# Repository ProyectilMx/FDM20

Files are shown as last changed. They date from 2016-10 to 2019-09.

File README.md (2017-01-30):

# FDM20
-This work is licensed under the Creative Commons Attribution-NonCommercial-NoDerivatives 4.0 International License.

-Esta obra está sujeta a la licencia Reconocimiento-NoComercial 4.0 Internacional de Creative Commons. Para ver una copia de esta licencia, visite https://creativecommons.org/licenses/by-nc-sa/4.0/

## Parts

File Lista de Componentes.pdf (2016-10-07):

Qty. | Nombre | Descripción | Categoría | Qty. | Nombre | Categoría
1 | Arduino Mega | Circuito de Control | Electrónica | 2 | PortaBaleroY | Impresión 3D
1 | RAMPS | Shield para Arduino | Electrónica | 4 | SoporteGuíaY | Impresión 3D
4 | A4988 | Drivers para Motor a Pasos | Electrónica | 1 | PortaMotorX | Impresión 3D
1 | SmartController | Pantalla LCD con perilla y lector de SD | Electrónica | 1 | ContraEjeX | Impresión 3D
3 | Endstop | Sensor de Final de Carrera | Electrónica | 2 | GuíasEjeZ | Impresión 3D
1 | Cama Caliente | Cama Caliente | Electrónica | 4 | PortaBaleroZ | Impresión 3D
1 | Fuente de Alimentación | Fuente de 12V a 30A 360W | Electrónica | 1 | CarroExtrusor | Impresión 3D
1 | Extensión USB | Extensión USB B de .5 m | Electrónica | 1 | PivotePortaTornillos | Impresión 3D
1 | Termistor | Termistor de 100KOhms | Electrónica | 1 | TapaTobera | Impresión 3D
2 | Cable Termistor | Cable Morado AWG22 | Electrónica | 1 | ContraPivote | Impresión 3D
1 | Switch Encendido | Switch LED 12V de 127V | Electrónica | 1 | Brazo | Impresión 3D
1 | Conector Interlock | Conector Alimentación | Electrónica | 1 | SmartController | Impresión 3D
3 | Zapatas Conector Interlock | Zapatas cable AWG20 para Conector Interloc | Electrónica | 1 | PortaSpool | Impresión 3D
3 | Zapatas Switch Encendido | Zapatas cable AWG20 para Switch Encendid | Electrónica | 2 | Separador Endstops | Impresión 3D
13 | Zapatas Fuente | Zapatas para Fuente de Alimentación,RAMP | Electrónica | 4 | SeguroGuiaZ | CorteLaser MDF
1 | Cable Tierra Conector-Fuente | Cable Negro AWG20 de 8 cm | Electrónica | 2 | MarcoSoporteLaterialInferior | CorteLaser MDF
1 | Cable Neutro Conector-Fuent | Cable Negro AWG20 de 9 cm | Electrónica | 2 | MarcoSoporteLaterialSuperio | CorteLaser MDF
1 | Cable Línea Conector-Switch | Cable Rojo AWG20 de 23 cm | Electrónica | 1 | BasePrincipal | CorteLaser MDF
1 | Cable Línea Switch-Fuente | Cable Rojo AWG20 de 24 cm | Electrónica | 1 | PanelFrontal | CorteLaser MDF
1 | Cable Neutro Switch-Fuente | Cable Negro AWG20 de 23 cm | Electrónica | 1 | PanelTrasero | CorteLaser MDF
2 | Cable Bicolor Fuente-RAMPS | Cable Bicolor AWG20 de 25 cm | Electrónica | 1 | PanelIzquierdo | CorteLaser MDF
1 | Household Dupont Doble | Household doble dupont AWG22 | Electrónica | 1 | PanelDerecho | CorteLaser MDF
2 | Dupont | Dupont AWG22 | Electrónica | 1 | MarcoSoporteFrontal | CorteLaser MDF
3 | Cables Endstops | Cable para Endstop | Electrónica | 1 | MarcoSoporteSensor | CorteLaser MDF
3 | Cable NEMA17 | Cable para NEMA17 corto | Electrónica | 1 | BasePrincipal Superior | CorteLaser MDF
1 | Cable NEMA17 | Cable para NEMA17 mediano | Electrónica | 1 | Base Madera Cama | CorteLaser MDF
1 | Cable NEMA17 | Cable para NEMA17 largo | Electrónica | 1 | PortaMotorY | CorteLaser MDF
1 | Cable Bicolor CamaCaliente | Cable Bicolor AWG20 | Electrónica | 1 | PortaMotorY Refuerzo | CorteLaser MDF
1 | Ventilador | Ventilador de 12V d 40mmx40mm | Electromecánica | 1 | PortaMotorY Lateral1 | CorteLaser MDF
5 | NEMA17 | Motor a Pasos NEMA 17 | Electromecánica | 1 | PortaMotorY Lateral2 | CorteLaser MDF
1 | Morral | Morral de Entrega para Kits | Kit | 4 | SeguroBanda | CorteLaser MDF
1 | HotEnd | HotEnd para extrusor | Electromecánica
12 | Rodamientos Lineales | Rodamiento Lineal LM8UU | Mecánica
3 | Balero 623 | Balero 623 | Mecánica | Qty. | Tornillería
1 | Balero 624 | Balero 624 | Mecánica | 9 | M3x30
2 | Polea Dentada | Polea Dentada T2 16 dientes 5 mm | Mecánica | 110 | Tuerca M3
1 | Banda X | Banda T2 corta | Mecánica | 10 | Tuerca M3 Seguridad
1 | Banda Y | Banda T2 larga | Mecánica | 81 | M3x16
2 | Guías Y | Guía de Acero Inoxidable de 8 mm 272 mm | Mecánica | 138 | Rondana M3
2 | Guías X | Guía de Acero Inoxidable de 8 mm 384 mm | Mecánica | 3 | M3x12
2 | Guías Z | Guía de Acero Inoxidable de 8 mm 412 mm | Mecánica | 16 | M3x10
2 | Cople Flexible Z | Cople Flexible de 5 - 8 mm | Mecánica | 8 | M3x40
4 | Resortes #26 | Resortes #26 para cama caliente | Mecánica | 6 | Rondana M3 Grande
1 | Vidrio | Vidrio de 3mm de 21.5 x 20 cm | Mecánica | 7 | M3x20
2 | Esparrágo Acero Inoxidable | Esparrago de Acero Inoxidable de 385 mm | Mecánica | 14 | M3x25
1 | Engrane Estriado | Engrane Estriado para el Extrusor | Mecánica | 1 | Tuerca M4
2 | Resortes #131 | Resortes #131 para Extrusor | Mecánica | 1 | M4x16
1 | Manguera Teflon | Manguera de Teflon de 3mm | Mecánica | 2 | M3x6
3 | Grapas Manguera | Grapas para manguera de teflon | Mecánica | 2 | Tuerca M8
1 | Gusano para cable | Gusano para cable de 1.5 m | Mecánica
1 | Separador de 10 mm | Separador Ventilador para Endstop | Mecánica
1 | Cable USB | Cable USB A-B de 1.8 m | Kit
1 | Interlock | Cable de Alimentación | Kit
1 | Memoria SD | Memoria SD de 4 GB | Kit

# Lista de Componentes

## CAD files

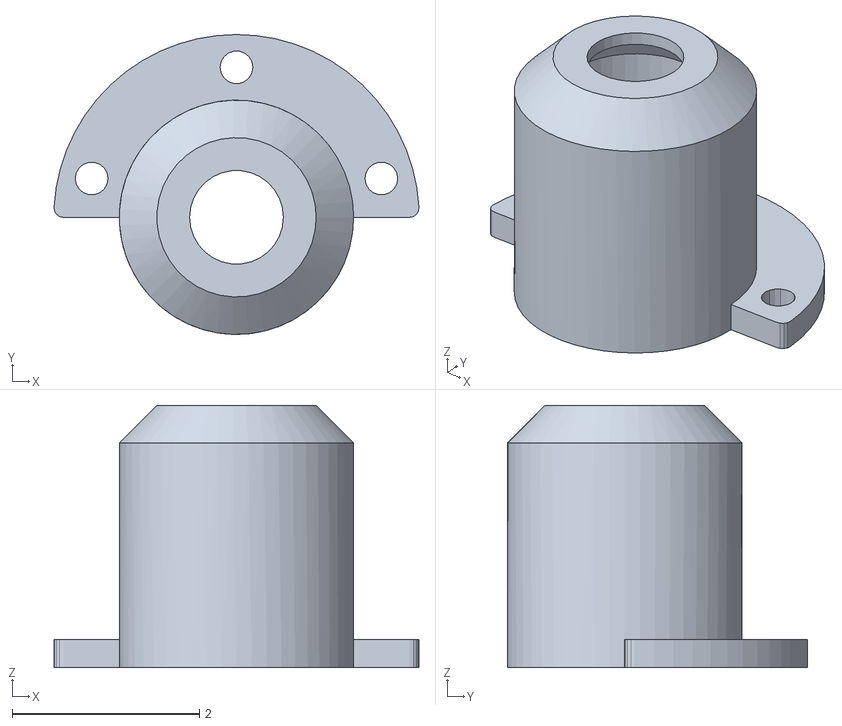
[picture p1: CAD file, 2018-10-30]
STL/FDM20-Ensamble-PortaBalerosZ-Barril.stl
3.89 x 3.20 x 2.80

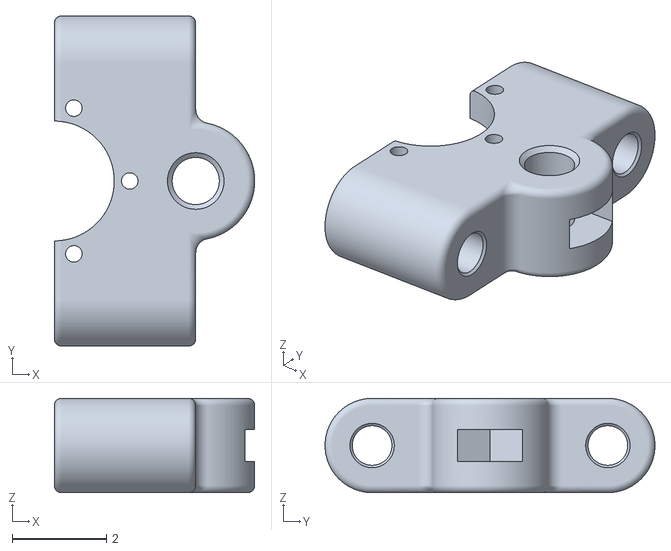
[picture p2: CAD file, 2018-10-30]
STL/FDM20-Ensamble-PortaBalerosZ-Guias.stl
4.25 x 7.00 x 2.00

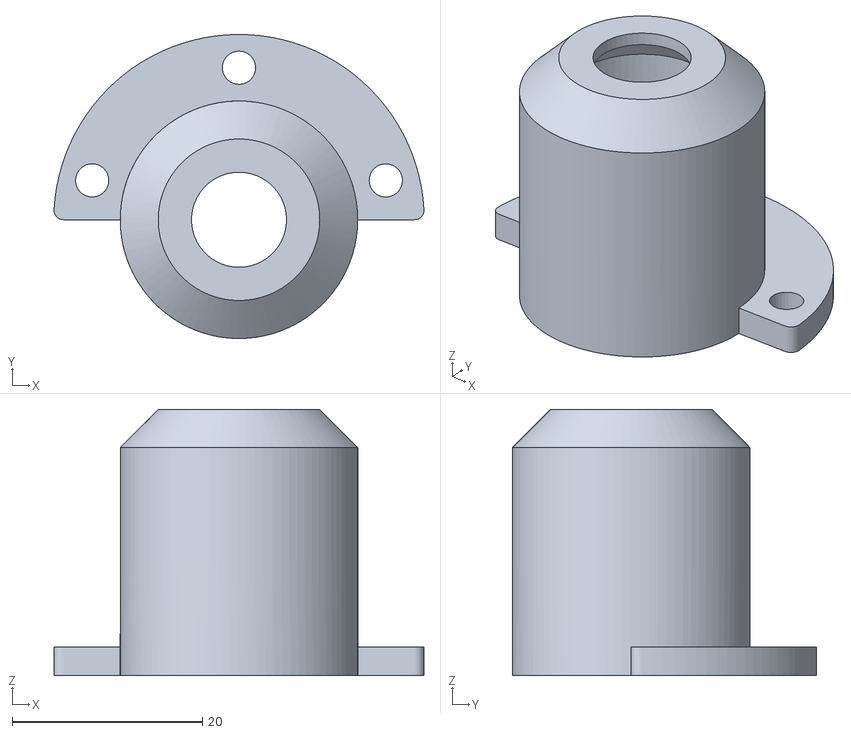
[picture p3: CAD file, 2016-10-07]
STL/FDM20-Ensamble-PortaBalerosZ-Parte1.stl
38.9 x 32.0 x 28.0

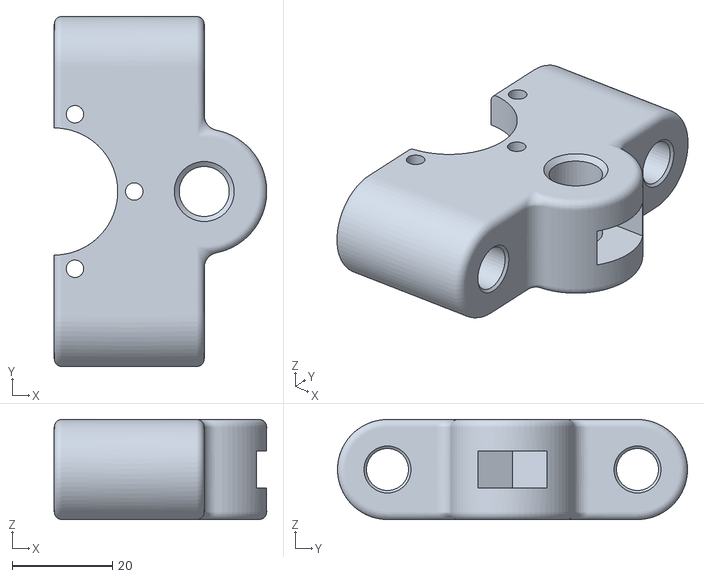
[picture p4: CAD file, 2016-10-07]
STL/FDM20-Ensamble-PortaBalerosZ-Parte2.stl
42.5 x 70.0 x 20.0

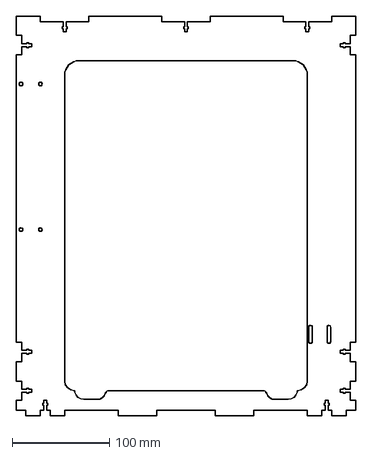
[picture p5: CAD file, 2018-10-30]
DXF/FDM20-BasePrincipal-MarcoSoporte-Sensor.dxf
350.0 x 412.0 mm

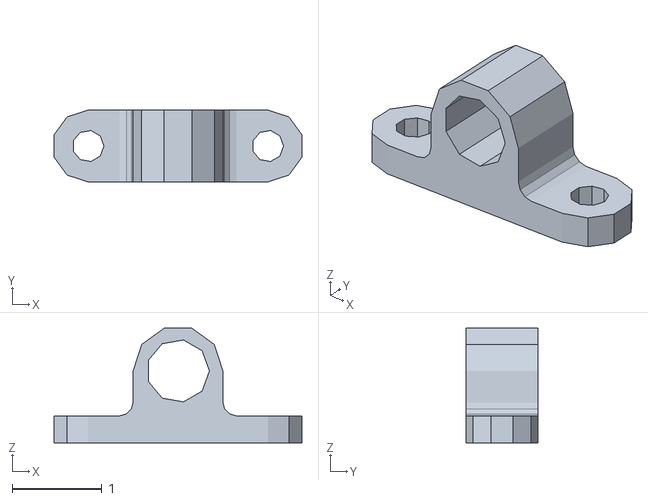
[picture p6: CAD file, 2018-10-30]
STL/FDM20-GuiaFilamento-Superior.stl
2.76 x 0.8 x 1.28

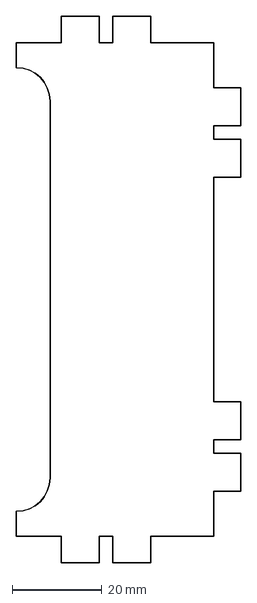
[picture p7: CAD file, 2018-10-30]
DXF/FDM20-BasePrincipal-MarcoSoporte-LaterialSuperior.dxf
50.0 x 122.0 mm

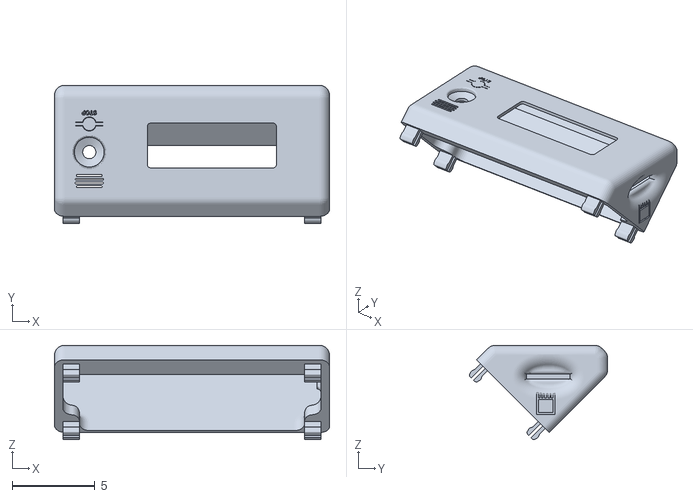
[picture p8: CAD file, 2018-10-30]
STL/FDM20-SmartController.stl
16.6 x 8.35 x 5.70

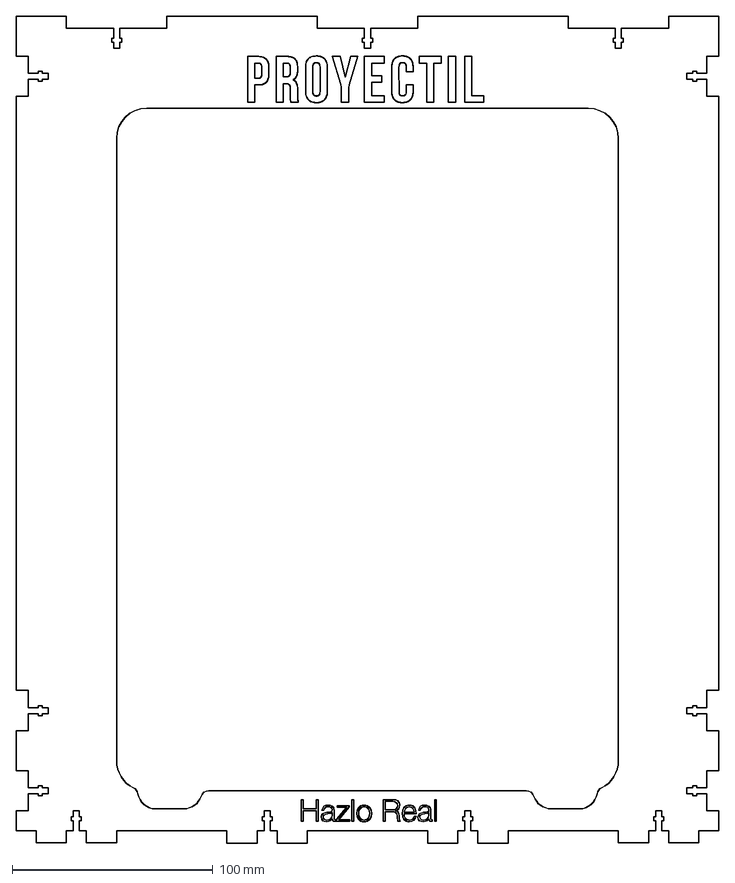
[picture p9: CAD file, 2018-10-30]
DXF/FDM20-BasePrincipal-MarcoSoporte-Frontal.dxf
350.0 x 412.0 mm

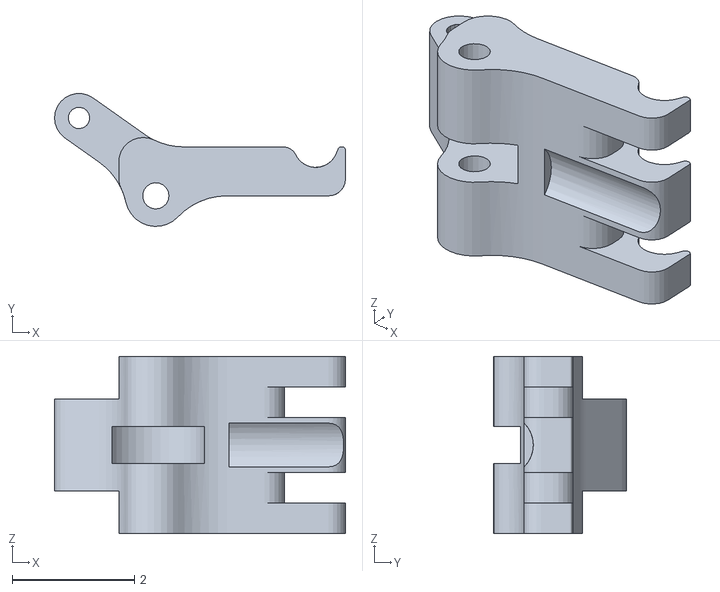
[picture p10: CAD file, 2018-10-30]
STL/FDM20-Extrusor-BrazoDePresion.stl
4.76 x 2.17 x 2.90

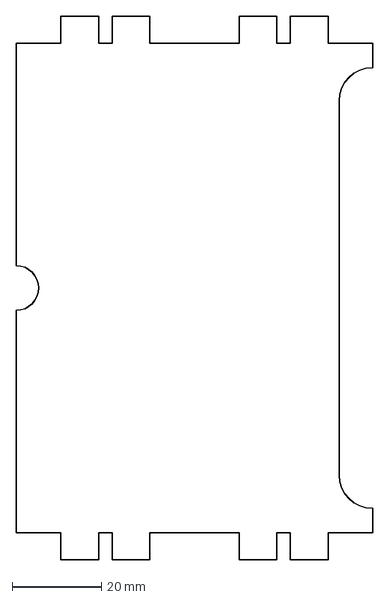
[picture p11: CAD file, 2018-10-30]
DXF/FDM20-BasePrincipal-MarcoSoporte-LaterialInferior.dxf
80.0 x 122.0 mm

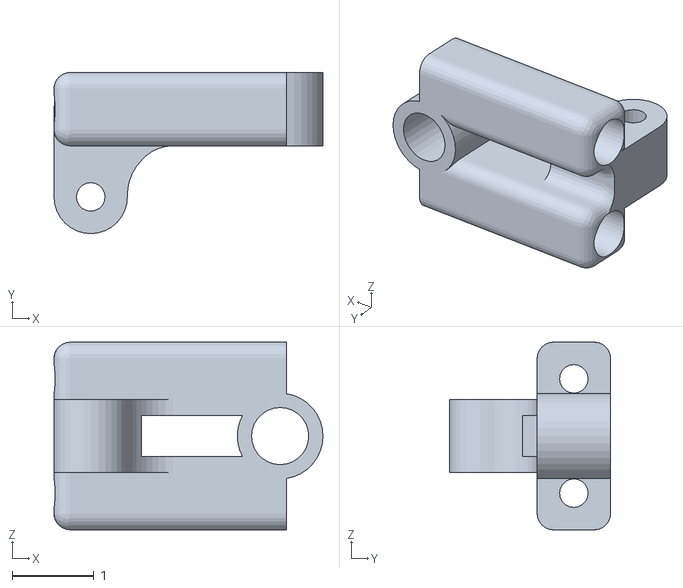
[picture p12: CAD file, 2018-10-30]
STL/FDM20-Extrusor-PivotePortaTornillos.stl
3.30 x 1.98 x 2.30

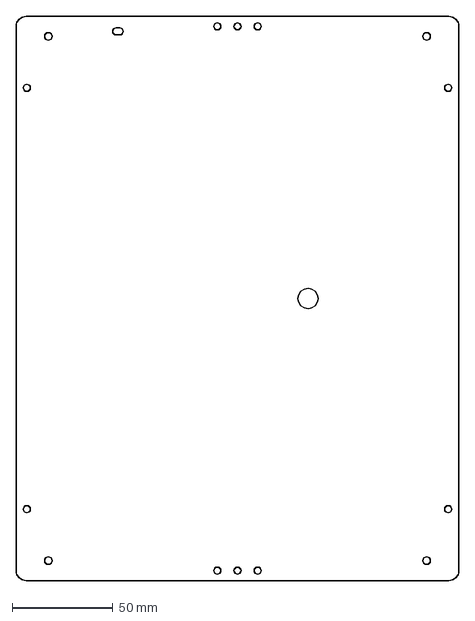
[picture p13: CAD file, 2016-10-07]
DXF/FDM20-BaseMaderaCama.dxf
219.6 x 280.0 mm

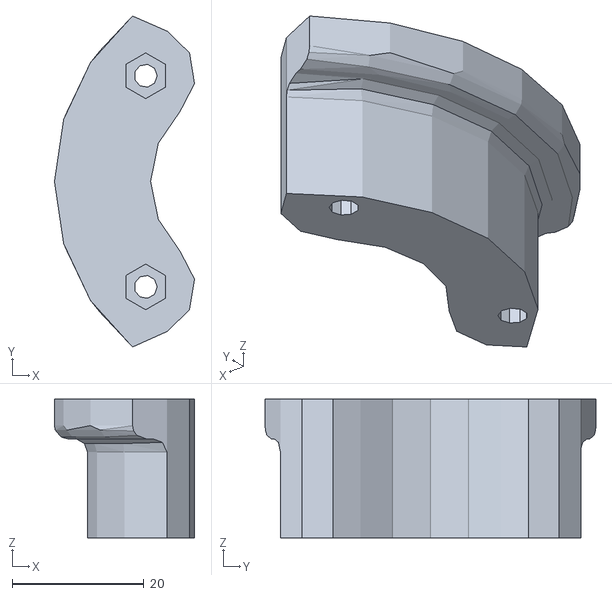
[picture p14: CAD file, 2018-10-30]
STL/FDM20-PortaSpool.stl
21.2 x 50.2 x 21.0

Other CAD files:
DXF/FDM20-BasePrincipal-Base.dxf
DXF/FDM20-BasePrincipal-IzquierdaInterruptor.dxf
STL/FDM20-BaseGuiasY.stl
DXF/FDM20-BasePrincipal-DerechoUSB.dxf
DXF/FDM20-BasePrincipal-FrontalLCD.dxf
DXF/FDM20-BasePrincipal-MarcoSoporte-Superior.dxf
DXF/FDM20-BasePrincipal-SeguroGuiaZ.dxf
DXF/FDM20-BasePrincipal-TraseraConector.dxf
DXF/FDM20-PortaMotorY-Lateral.dxf
DXF/FDM20-PortaMotorY-Principal.dxf
DXF/FDM20-PortaMotorY-Refuerzo.dxf
DXF_old/FDM20-BasePrincipal-Base.dxf
DXF_old/FDM20-BasePrincipal-DerechoUSB.dxf
DXF_old/FDM20-BasePrincipal-FrontalLCD.dxf
DXF_old/FDM20-BasePrincipal-IzquierdaInterruptor.dxf
DXF_old/FDM20-BasePrincipal-MarcoSoporte-Frontal.dxf
DXF_old/FDM20-BasePrincipal-MarcoSoporte-LaterialInferior.dxf
DXF_old/FDM20-BasePrincipal-MarcoSoporte-LaterialSuperior.dxf
DXF_old/FDM20-BasePrincipal-MarcoSoporte-Sensor.dxf
DXF_old/FDM20-BasePrincipal-MarcoSoporte-Superior.dxf
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

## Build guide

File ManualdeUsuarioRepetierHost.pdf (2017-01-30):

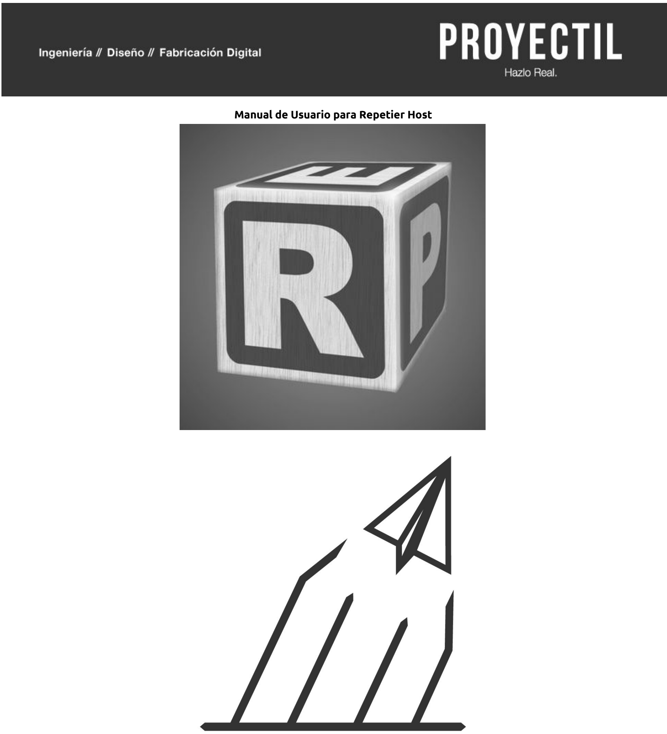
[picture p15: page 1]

Manual de Usuario para Repetier Host

Índice

## Configuración Repetier Host Slic3r Conociendo la Interfaz Gráfica Navegación del entorno 3D Opciones del modelo 3D Slicer Print Preview

## Configuración

Después de instalar el software, lo primero que se debe hacer es realizar la configuración de la impresora tanto en Repetier Host como en Slic3r. A continuación se presentan los pasos a seguir para la configuración en ambos softwares:

## Repetier Host

En Repetier Host seleccionar del menú “Config” -> “Printer Settings” o dar click en el botón

Al hacerlo aparecerá el siguiente recuadro con distintas opciones. Es necesario contar con las mismas configuraciones mostradas en los recuadros.

A) Connection: Aquí la opción del Puerto de comunicación dependerá del sistema operativo.

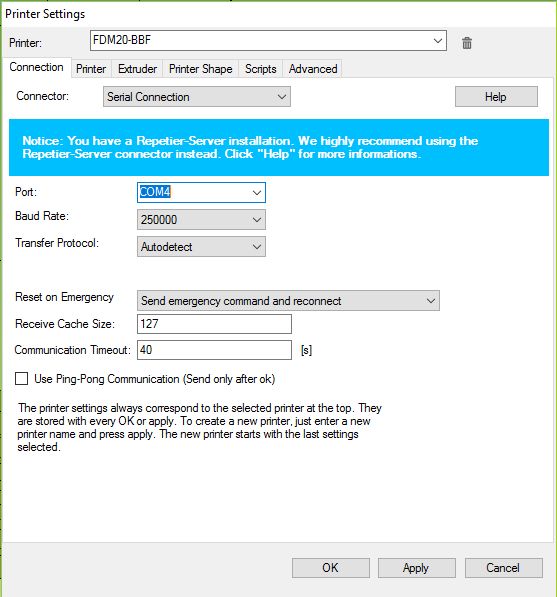
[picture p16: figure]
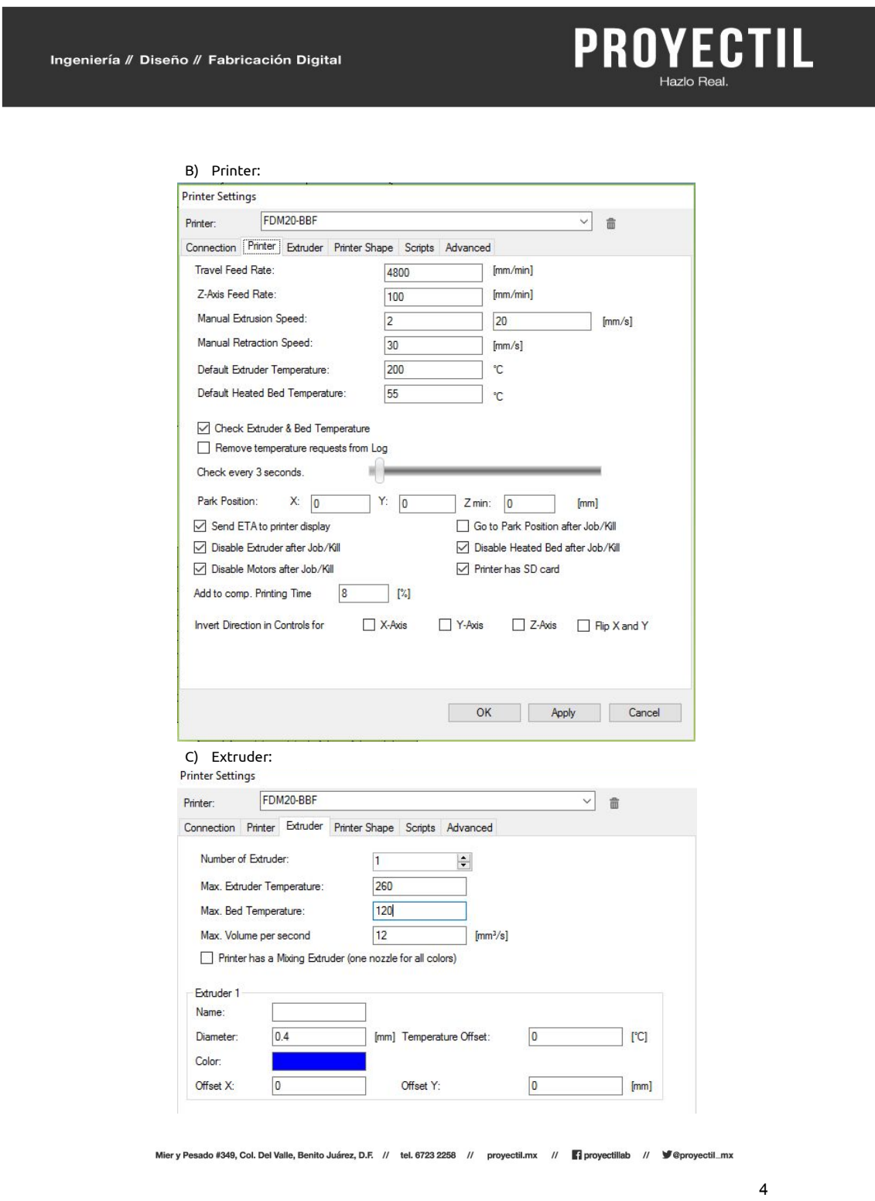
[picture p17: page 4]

B) Printer:
C) Extruder:

D) Printer Shape:

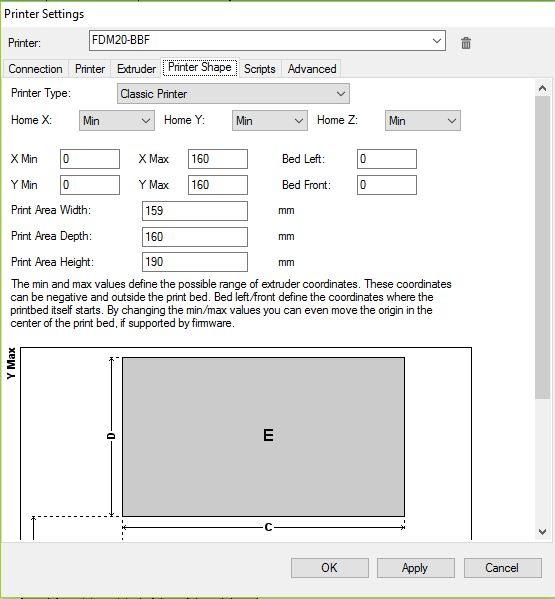
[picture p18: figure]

E) Scripts: En esta pestaña no se deberá modificar la configuración por default.
F) Advanced: En esta pestaña no se deberá modificar la configuración por default.

Una vez realizados todos los cambios es necesario apretar el botón Apply en la parte inferior del recuadro y posteriormente hacer click en el botón OK.

## Slic3r

Ahora es necesario configurar Slic3r para el correcto procesamiento de los modelos a imprimir. Para esto es necesario ir a la pestaña Slic3r del lado derecho del Software, justo debajo del botón “Printer Settings” utilizado para la configuración de Repetier Host.

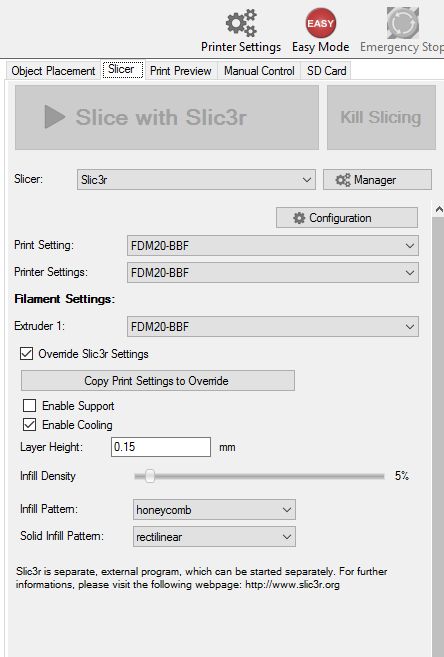
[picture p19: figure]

Una vez en esta pestaña es necesario seleccionar en Slicer la opción Slic3r. Posteriormente se deberá

abrir la configuración de Slic3r apretando el botón | .

Al hacer esto se abrirá una nueva ventana de configuración del software de procesamiento Slic3r. En esta ventana, debemos de ir al menú “File” -> “Load Config Bundle” y deberemos de seleccionar el archivo de configuración FDM20.ini entregado por Proyectil durante el taller. En caso de no contar con este archivo, se podrá descargar desde la página de GitHub. (https://github.com/ProyectilMx/FDM20)

## Conociendo la Interfaz Gráfica

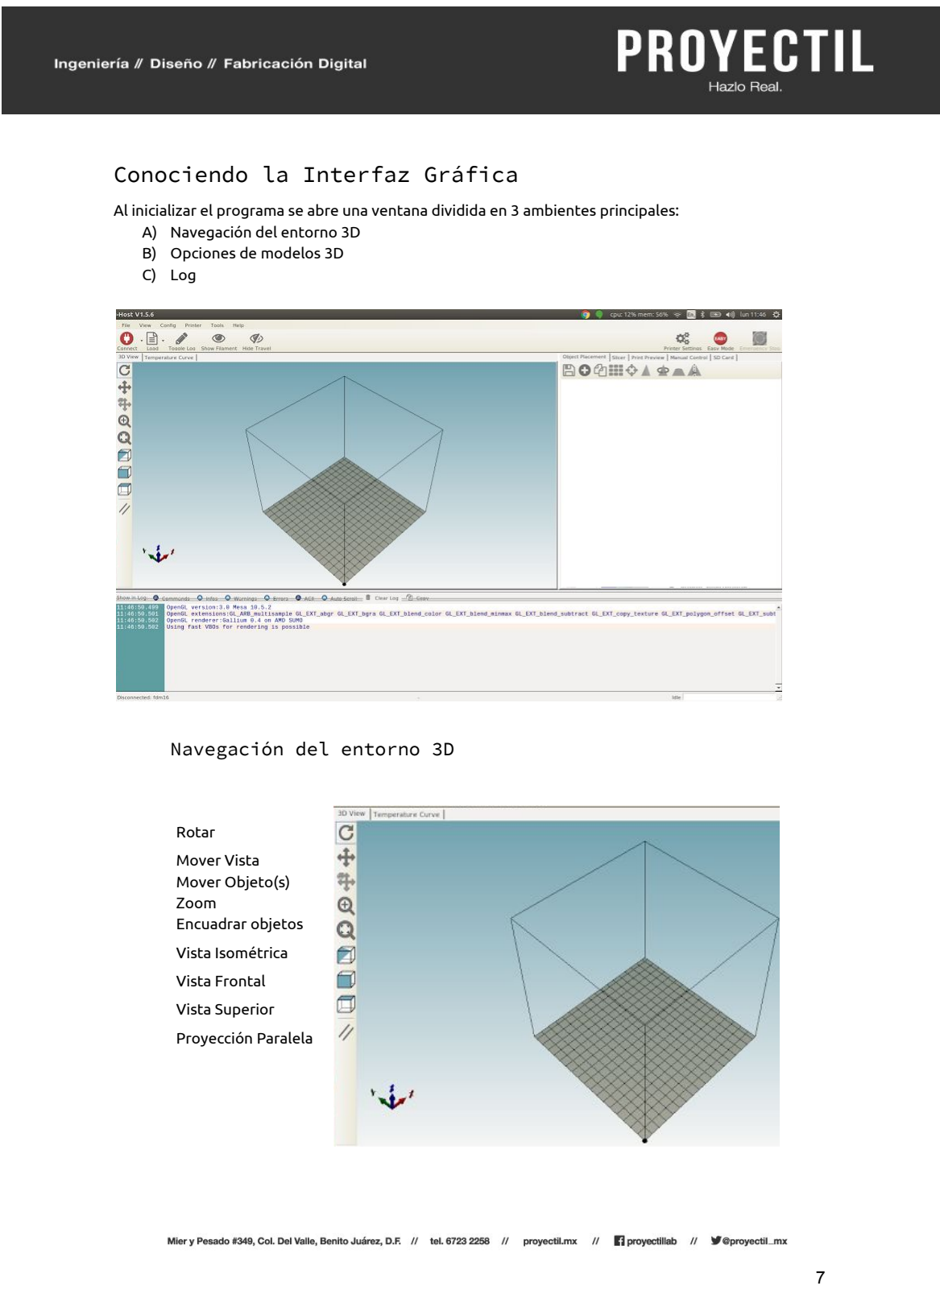
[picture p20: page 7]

Al inicializar el programa se abre una ventana dividida en 3 ambientes principales:
A) Navegación del entorno 3D
B) Opciones de modelos 3D
C) Log

## Navegación del entorno 3D

Rotar
Mover Vista
Mover Objeto(s)
Zoom
Encuadrar objetos
Vista Isométrica
Vista Frontal
Vista Superior
Proyección Paralela

## Opciones del modelo 3D

Para agregar el modelo, se cuenta con la opción Drag and Drop, o en caso se debe apretar el

botón con el símbolo de más.

Al abrir un modelo, aparecerá un nuevo grupo de objetos con el modelo a modo de lista. Es posible agregar varios modelos al mismo tiempo. Además en la sección de navegación del entorno 3D se mostrará el modelo o los modelos agregados, como se muestra en la siguiente imagen.

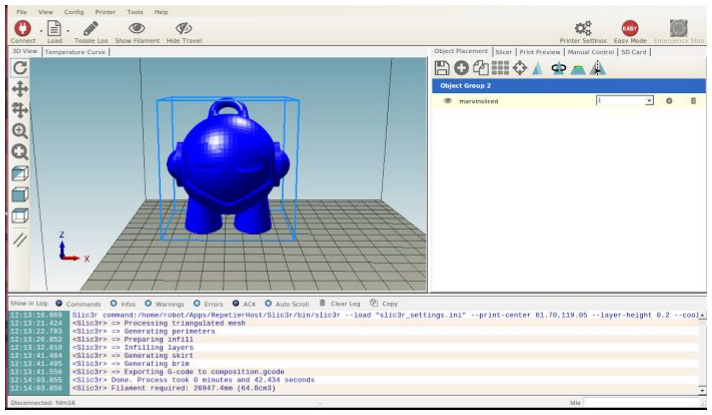
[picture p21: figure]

## Slicer

Posteriormente es necesario cambiar a la pestaña de Slicer y verificar que las configuraciones de Proyectil Mx estén seleccionadas.

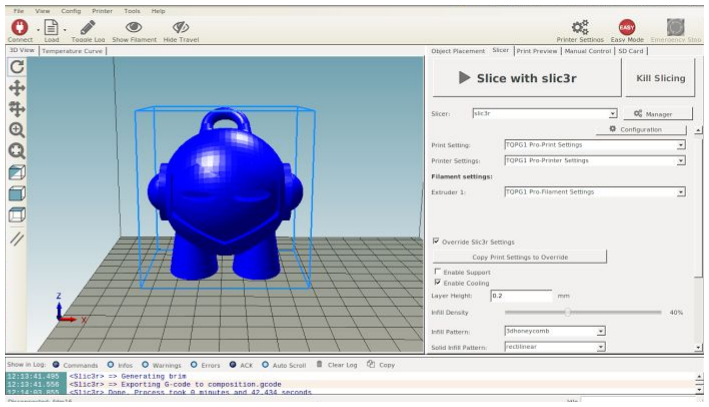
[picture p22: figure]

Una vez revisadas las configuraciones se debe apretar el botón Slice with slic3r.

## Print Preview

En automático, el programa comenzará con el procesamiento del modelo y al terminar se
| cambiará a la pestaña Print Preview. En esta pestaña se encuentran 4 botones en la parte
| superior y en la inferior se muestra información de tiempos aproximados de impresión,
| cantidad de material a utilizar, además de permitir la visualización de las rutas a seguir por
| parte de la impresora y/o las capas que conformarán el modelo impreso.
| Los botones permiten iniciar la impresión si la impresora se encuentra conectada a la
| computadora (Print), editar el código g que se enviará a la impresora (Edit G-Code) y guardar
| el archivo (Save to File / Save for SD Print).
| Al apretar Save for SD Print, en automático se agrega el código G de inicio y final que está
| configurado en Repetier. El botón de Save to File, solamente lo guarda con la finalidad de
| volverlo a abrir en repetier y mandar a imprimir desde la computadora.
| Una vez guardado el archivo, se copia en la memoria SD, y se manda a imprimir directo en la
| impresora.

Listo! Ahora ya puedes imprimir tus modelos!

Nota:
Si se desea conocer más sobre el funcionamiento de Repetier Host y/o alguna de sus
opciones, | acudir | a | la | página | de | tutoriales | de | Repetier-Host.
http://www.repetier.com/tutorials/

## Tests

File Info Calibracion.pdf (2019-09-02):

# Instrucciones de calibración de FDM//20

La calibración, funciona como cualquier máquina CNC, como guía se enlistan los siguientes pasos:
- Alistar un papel para la calibración.
- Mandar a home el extrusor.
- Antes de que llegue a 0 en Z colocar el papel entre el extrusor y la cama caliente. (Para una correcta calibración, se debe calentar el extrusor para evitar que residuos de plástico en la punta del mismo modifiquen la distancia entre el hotend y la cama caliente.)
!!!!ES IMPORTANTE REALIZAR ESTOS PASOS CON PRECAUCIÓN DEBIDO A LA TEMPERATURA DEL EXTRUSOR!!!!!!
- Verificar que el hotend roce el papel sin que lo rompa y aún permita su movimiento. En caso
contrario | ajustar | el | tornillo | correspondiente
utilizando las pinzas de punta para detener la tuerca de seguridad.
- Elevar un par de milímetros el extrusor, y desplazar al otro extremo del Eje X/Y.
- Bajar el extrusor a 0 en el eje Z.
- Repetir pasos del 3 al 6, hasta verificar al menos 2 veces en cada punto que la punta del Hotend roce el papel.

Listo, ya no debería existir ningún problema para imprimir; para asegurar, sería necesario mandar a extruir y una vez que se vea como sale el plástico, ya están listos para mandar a imprimir.

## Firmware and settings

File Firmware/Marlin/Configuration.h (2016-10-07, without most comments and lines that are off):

#define CONFIGURATION_H
#include "boards.h"
#include "macros.h"
#if ENABLED(USE_AUTOMATIC_VERSIONING)
  #include "_Version.h"
#else
  #include "Version.h"
#endif
#define STRING_CONFIG_H_AUTHOR "(none, default config)" // Who made the changes.
#define SHOW_BOOTSCREEN
#define STRING_SPLASH_LINE1 SHORT_BUILD_VERSION // will be shown during bootup in line 1
#define SERIAL_PORT 0
#define BAUDRATE 250000
  #define MOTHERBOARD BOARD_RAMPS_14_EFB
#define CUSTOM_MACHINE_NAME "FDM 20"
#define EXTRUDERS 1
#define POWER_SUPPLY 1
#define TEMP_SENSOR_0 5
#define TEMP_SENSOR_1 0
#define TEMP_SENSOR_2 0
#define TEMP_SENSOR_3 0
#define TEMP_SENSOR_BED 1
#define MAX_REDUNDANT_TEMP_SENSOR_DIFF 10
#define TEMP_RESIDENCY_TIME 2  // (seconds)
#define TEMP_HYSTERESIS 3       // (degC) range of +/- temperatures considered "close" to the target one
#define TEMP_WINDOW     1       // (degC) Window around target to start the residency timer x degC early.
#define TEMP_BED_RESIDENCY_TIME 2  // (seconds)
#define TEMP_BED_HYSTERESIS 3       // (degC) range of +/- temperatures considered "close" to the target one
#define TEMP_BED_WINDOW     1       // (degC) Window around target to start the residency timer x degC early.
#define HEATER_0_MINTEMP 5
#define HEATER_1_MINTEMP 5
#define HEATER_2_MINTEMP 5
#define HEATER_3_MINTEMP 5
#define BED_MINTEMP 5
#define HEATER_0_MAXTEMP 275
#define HEATER_1_MAXTEMP 275
#define HEATER_2_MAXTEMP 275
#define HEATER_3_MAXTEMP 275
#define BED_MAXTEMP 150
#define PIDTEMP
#define BANG_MAX 255 // limits current to nozzle while in bang-bang mode; 255=full current
#define PID_MAX BANG_MAX // limits current to nozzle while PID is active (see PID_FUNCTIONAL_RANGE below); 255=full current
  #define PID_FUNCTIONAL_RANGE 10 // If the temperature difference between the target temperature and the actual temperature
  #define PID_INTEGRAL_DRIVE_MAX PID_MAX  //limit for the integral term
  #define K1 0.95 //smoothing factor within the PID
  #define  DEFAULT_Kp 22.2
  #define  DEFAULT_Ki 1.08
  #define  DEFAULT_Kd 114
#define MAX_BED_POWER 255 // limits duty cycle to bed; 255=full current
#define PREVENT_DANGEROUS_EXTRUDE
#define PREVENT_LENGTHY_EXTRUDE
#define EXTRUDE_MINTEMP 170
#define EXTRUDE_MAXLENGTH (X_MAX_LENGTH+Y_MAX_LENGTH) //prevent extrusion of very large distances.
#define THERMAL_PROTECTION_HOTENDS // Enable thermal protection for all extruders
#define THERMAL_PROTECTION_BED     // Enable thermal protection for the heated bed
#define USE_XMIN_PLUG
#define USE_YMIN_PLUG
#define USE_ZMIN_PLUG
#define ENDSTOPPULLUPS // Comment this out (using // at the start of the line) to disable the endstop pullup resistors
const bool X_MIN_ENDSTOP_INVERTING = true; // set to true to invert the logic of the endstop.
const bool Y_MIN_ENDSTOP_INVERTING = true; // set to true to invert the logic of the endstop.
const bool Z_MIN_ENDSTOP_INVERTING = true; // set to true to invert the logic of the endstop.
const bool X_MAX_ENDSTOP_INVERTING = false; // set to true to invert the logic of the endstop.
const bool Y_MAX_ENDSTOP_INVERTING = false; // set to true to invert the logic of the endstop.
const bool Z_MAX_ENDSTOP_INVERTING = false; // set to true to invert the logic of the endstop.
const bool Z_MIN_PROBE_ENDSTOP_INVERTING = false; // set to true to invert the logic of the endstop.
#define Z_MIN_PROBE_USES_Z_MIN_ENDSTOP_PIN
#define X_ENABLE_ON 0
#define Y_ENABLE_ON 0
#define Z_ENABLE_ON 0
#define E_ENABLE_ON 0 // For all extruders
#define DISABLE_X false
#define DISABLE_Y false
#define DISABLE_Z false
#define DISABLE_E false // For all extruders
#define DISABLE_INACTIVE_EXTRUDER true //disable only inactive extruders and keep active extruder enabled
#define INVERT_X_DIR false
#define INVERT_Y_DIR false
#define INVERT_Z_DIR true
#define INVERT_E0_DIR false
#define INVERT_E1_DIR false
#define INVERT_E2_DIR false
#define INVERT_E3_DIR false
#define X_HOME_DIR -1
#define Y_HOME_DIR -1
#define Z_HOME_DIR -1
#define min_software_endstops true // If true, axis won't move to coordinates less than HOME_POS.
#define max_software_endstops true  // If true, axis won't move to coordinates greater than the defined lengths below.
#define X_MIN_POS 0
#define Y_MIN_POS 0
#define Z_MIN_POS 0
#define X_MAX_POS 160
#define Y_MAX_POS 160
#define Z_MAX_POS 190
#define Z_MIN_PROBE_REPEATABILITY_TEST  // If not commented out, Z Probe Repeatability test will be included if Auto Bed Leveling is Enabled.
#define HOMING_FEEDRATE {50*60, 50*60, 4*60, 0}  // set the homing speeds (mm/min)
#define DEFAULT_AXIS_STEPS_PER_UNIT   {80,80,2560,142}  // default steps per unit for Ultimaker
#define DEFAULT_MAX_FEEDRATE          {300, 300, 10, 40}    // (mm/sec)
#define DEFAULT_MAX_ACCELERATION      {3000,3000,100,10000}    // X, Y, Z, E maximum start speed for accelerated moves. E default values are good for Skeinforge 40+, for older versions raise them a lot.
#define DEFAULT_ACCELERATION          3000    // X, Y, Z and E acceleration in mm/s^2 for printing moves
#define DEFAULT_RETRACT_ACCELERATION  3000    // E acceleration in mm/s^2 for retracts
#define DEFAULT_TRAVEL_ACCELERATION   500    // X, Y, Z acceleration in mm/s^2 for travel (non printing) moves
#define DEFAULT_XYJERK                20.0    // (mm/sec)
#define DEFAULT_ZJERK                 0.4     // (mm/sec)
#define DEFAULT_EJERK                 5.0    // (mm/sec)
#define CUSTOM_M_CODES
  #define DEFAULT_KEEPALIVE_INTERVAL 2 // Number of seconds between "busy" messages. Set with M113.
#define PLA_PREHEAT_HOTEND_TEMP 180
#define PLA_PREHEAT_HPB_TEMP 70
#define PLA_PREHEAT_FAN_SPEED 0   // Insert Value between 0 and 255
#define ABS_PREHEAT_HOTEND_TEMP 240
#define ABS_PREHEAT_HPB_TEMP 110
#define ABS_PREHEAT_FAN_SPEED 0   // Insert Value between 0 and 255
#define LANGUAGE_INCLUDE GENERATE_LANGUAGE_INCLUDE(es)
#define DISPLAY_CHARSET_HD44780_JAPAN        // this is the most common hardware
#define ULTRA_LCD   // Character based
#define SDSUPPORT
#define SD_CHECK_AND_RETRY
#define REVERSE_MENU_DIRECTION
#define SPEAKER
#define LCD_FEEDBACK_FREQUENCY_DURATION_MS 50
#define LCD_FEEDBACK_FREQUENCY_HZ 200
#define REPRAP_DISCOUNT_SMART_CONTROLLER
#define SOFT_PWM_SCALE 0
#define DEFAULT_NOMINAL_FILAMENT_DIA 3.00  //Enter the diameter (in mm) of the filament generally used (3.0 mm or 1.75 mm) - this is then used in the slicer software.  Used for sensor reading validation
#include "Configuration_adv.h"
#include "thermistortables.h"

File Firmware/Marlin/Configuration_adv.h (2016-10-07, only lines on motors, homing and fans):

#define CONTROLLERFAN_PIN -1 //Pin used for the fan to cool controller (-1 to disable)
#define EXTRUDER_0_AUTO_FAN_PIN -1
#define EXTRUDER_1_AUTO_FAN_PIN -1
#define EXTRUDER_2_AUTO_FAN_PIN -1
#define EXTRUDER_3_AUTO_FAN_PIN -1
#define ENDSTOPS_ONLY_FOR_HOMING // If defined the endstops will only be used for homing
#define X_HOME_BUMP_MM 5
#define Y_HOME_BUMP_MM 5
#define Z_HOME_BUMP_MM 2
#define HOMING_BUMP_DIVISOR {2, 2, 4}  // Re-Bump Speed Divisor (Divides the Homing Feedrate)
#define MICROSTEP_MODES {16,16,16,16,16} // [1,2,4,8,16]
#define DIGIPOT_MOTOR_CURRENT {135,135,135,135,135} // Values 0-255 (RAMBO 135 = ~0.75A, 185 = ~1A)
#define DIGIPOT_I2C_MOTOR_CURRENTS {1.0, 1.0, 1.0, 1.0, 1.0, 1.0, 1.0, 1.0}

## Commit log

2016-10-07 This commit involves all the updates until october 2016 for the FDM//20
    [Configuration.h, Configuration_adv.h, FDM20-BandaX-01.0001.ipt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]
2016-10-07 Files removed, in order to update them
    [Configuration.h, Configuration_adv.h, FDM20-BasdePrincipal-SeguroBanda-.dxf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]
2016-10-07 All files updated til October 2016
    [Configuration.h, Configuration_adv.h, FDM20-BandaX-01.0001.ipt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]
2016-10-16 Update Octuber 16
    [FDM20-BandaX-01.0001.ipt, FDM20-BandaX-01.0002.ipt, FDM20-BandaX-01.ipt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]
2017-01-30 Add files via upload
    Manual de Usuario Repetier-Host
2017-07-07 Add files via upload
    Adaptador necesario para imprimir con plásticos flexibles
    [FDM20-Adaptador para NinjaFlex.stl]
2018-10-30 Versión Q3 2018
    [Configuration.h, Configuration_adv.h]
2018-10-30 Version Q3 2018
    [FDM20-Adaptador para NinjaFlex.stl, FDM20-BaseGuiasY.stl, FDM20-BaseMaderaCama.dxf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]
2020-01-20 FW sin Cama Caliente
    Firmware para utilizar la impresora sin cama caliente. Es necesario desconectar la cama caliente de la alimentación para minimizar riesgos.

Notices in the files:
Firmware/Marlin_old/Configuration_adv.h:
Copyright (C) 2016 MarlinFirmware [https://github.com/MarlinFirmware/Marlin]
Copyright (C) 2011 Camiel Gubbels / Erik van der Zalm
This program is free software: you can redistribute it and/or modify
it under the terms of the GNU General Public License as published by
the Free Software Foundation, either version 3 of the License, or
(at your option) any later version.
